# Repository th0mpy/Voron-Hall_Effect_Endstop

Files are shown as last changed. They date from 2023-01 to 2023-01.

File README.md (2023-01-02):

XY Endstop

# Voron Design XY Endstop Board
Hall effect endstop board for X and Y axes

The Hall Effect board allows for contactless homing on the  X and Y axis on a Voron 2.When hall sensor reaches close to magnet it produces a voltage. The circuit then compares that with a reference voltage. The comparator flips based on threshold set using the trim pots.
Please follow following procedure to setup Hall Effect Board.
1) Make sure both the pots are centered.
2) Then take a magnet for x axis.Try both the poles. Find the pole of magnet that triggers sensor within 1 inch of magnet.
3) Install the X magnet into afterburner carriage.
4) Please repeat the same process for Y axis and then install it in zblock.

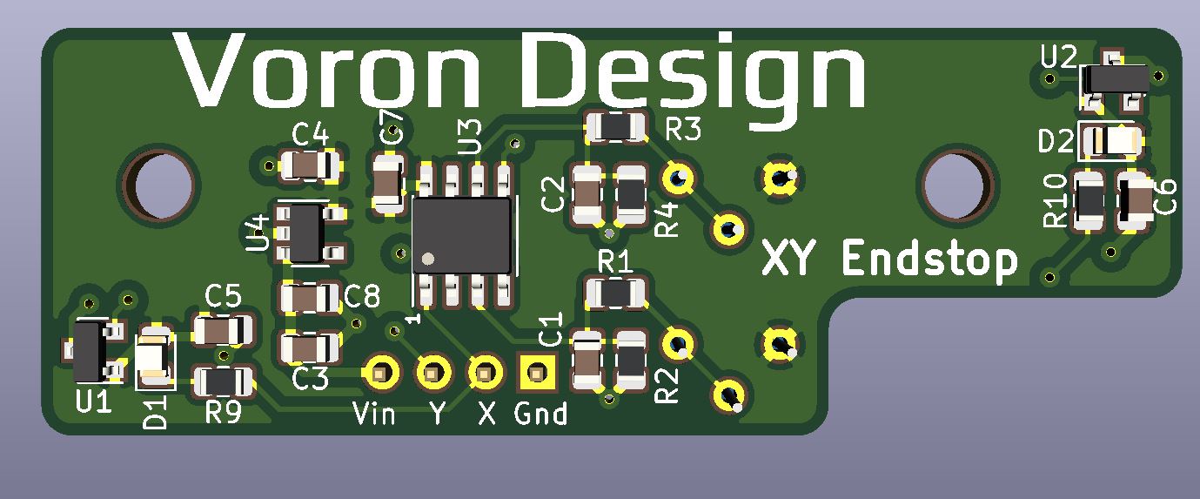
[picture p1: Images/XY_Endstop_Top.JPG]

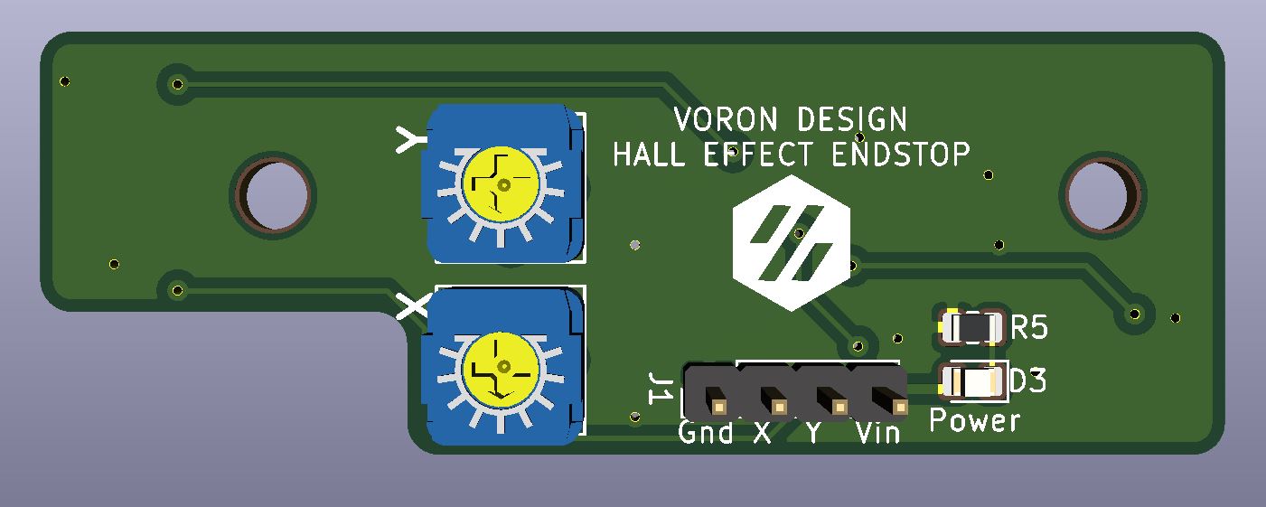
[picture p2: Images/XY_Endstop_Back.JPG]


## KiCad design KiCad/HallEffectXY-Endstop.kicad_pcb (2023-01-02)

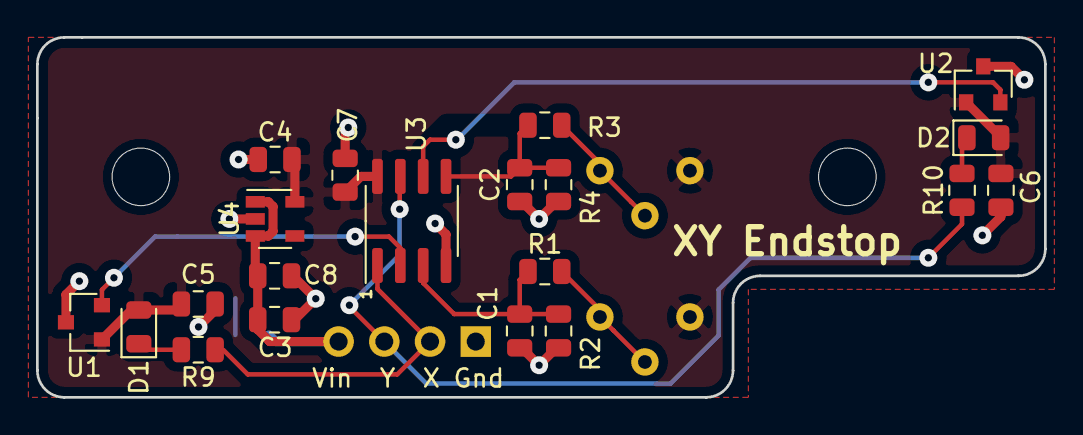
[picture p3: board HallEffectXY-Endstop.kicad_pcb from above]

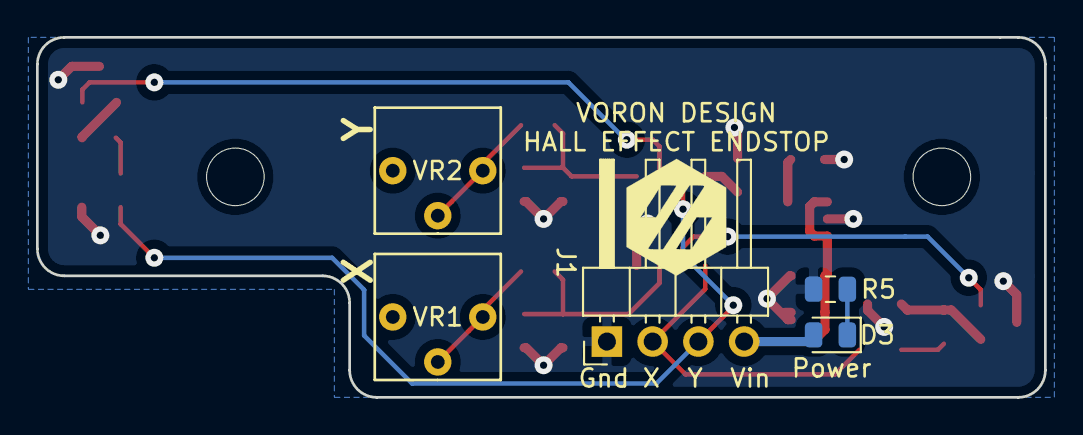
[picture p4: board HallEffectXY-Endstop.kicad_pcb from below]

Board: 2 copper layers, 56.0 x 20.0 mm, 25 parts (5 on the bottom side), 14 nets.

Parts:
C1, C2: 0.1uF; C_0805_2012Metric
C3, C4, C5, C6, C7: 1uF; C_0805_2012Metric
C8: 10uF; C_0805_2012Metric
D1, D2, D3: LED_0805; LED_0805_2012Metric
J1: CONN_01X04; PinHeader_1x04_P2.54mm_Horizontal
R1, R3, R5, R9, R10: 1.00K; R_0805_2012Metric
R2, R4: 10.0k; R_0805_2012Metric
U1, U2: SS39ET; SOT-23
U3: LM393; SOIC-8_3.9x4.9mm_P1.27mm
U4: AP2127K-3.3; SOT-23-5
VR1, VR2: 10.0K; CT6EP103

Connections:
+3V3: C4.1, C5.1, C6.1, C7.2, D1.2, D2.2, U1.1, U2.1, U3.8, U4.5, VR1.3, VR2.3
+5V: C3.1, C8.1, D3.2, J1.4, U4.1, U4.3
GND: C1.2, C2.2, C3.2, C4.2, C5.2, C6.2, C7.1, C8.2, J1.1, R2.2, R4.2, R5.1, U1.3, U2.3, U3.4, U4.2
unnamed: C1.1, R1.1, R2.1, U3.3
unnamed: C2.1, R3.1, R4.1, U3.5
unnamed: D1.1, R9.1
unnamed: D2.1, R10.1
unnamed: D3.1, R5.2
unnamed: R1.2, VR1.1, VR1.2
unnamed: R3.2, VR2.1, VR2.2
unnamed: U1.2, U3.2
unnamed: U2.2, U3.6
X_SIG: J1.2, R9.2, U3.1
Y_SIG: J1.3, R10.2, U3.7
